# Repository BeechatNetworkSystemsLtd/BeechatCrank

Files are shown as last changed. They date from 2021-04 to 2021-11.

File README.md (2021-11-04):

# Beechat Crank
## _The last charger you'll ever need_

BNSLTD

Beechat Crank is a human-powered, open-hardware, fully-waterproof, electricity generator.
The project was born out of the need to power electronics in all off-grid scenarios. We needed a way to power our devices in all weather conditions, and making a human-powered generator meant that problem could be solved. When we looked for a solution, we didn't find what we were looking for, so we decided to make it, and make it open source!

## Features

- High power (3A) USB-C IPX8 output
- 18650 3600 mAh battery (LG M36)
- Charging time of 4 hrs 24 min. to full charge with 10% efficiency loss at 4.5 Watts.
- Overcharge protection

## Parts

1. Beechat Crank is composed of the main device, which we call the _Heart_. It contains the battery, the generator and all the electronics (the handle is detachable) :
Heart

2. The _Pedal Case_ is an assembly which the _Heart_ can be attached in. which dramatically speeds up the charging from 2.5 hours to 25-30 minutes. This is achieved with reduction gears to, with the same revolutions per minute, generate more electricity.
Heart

## _Generator_ part
We have chosen the 35L048B1B motor with a mass of 88 grams, giving us us 450 mA for each phase of the coil and works at 5V. 
The wire leads are connected via female Molex connectors to the charging PCB board.

## _Heart_ parts

| Part no. | Part name | Quantity | Description | Link | Price |
| --- | --- | --- | --- | --- | --- |
| 01 | Body | 1 | Injection molded ABS/PC |
| 02 |  Lid | 1 | Injection molded ABS/PC
| 03 | Handle | 1 | Injection molded ABS/PC
| 04 | Light pipe | 1 | Transparent injection molded PC
| 05 | Motor | 1 | | [Link](https://aliexpress.com/item/4000827045633.html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,searchweb201602_,searchweb201603_) | $11
| 06 | Bearing | 1 | | [Link](http://manufacturer.ketanbearing.in/70745-NSKF686ADD-Bearing/) | $0.5
| 07 | PCB | 1 | |  | $6
| 08 | Battery holder | 1 | | [Link](https://aliexpress.com/item/4001063295116.html) | $0.09
| 09 | Lid O-Ring | 1 | | [Link]() | $0.95
| 10 | Bearing O-ring | 1 | | [Link](https://www.oringsandmore.com/silicone-o-rings-11-5-x-1mm-minimum-10-pcs/) | $0.08
| 10 | Adhesive | 1 | | | $8.36
| 11 | 10 mm M2 screws | 6 | | |
| 12 | 10 mm M3 screw | 1 | | |
|Total cost (excl. plastic parts and adhesive) | | | | | $18.62 

## _Heart_ PCB parts

All parts are under the "3_BOM and CPL" folder

## _Pedal Case_ parts

| Part no. | Part name | Quantity | Description | Link | Price |
| --- | --- | --- | --- | --- | --- |
| 01 | Sheet metal stand | 1 | Stainless steel sheet metal bend |
| 02 |  Plastic cover | 1 | Injection molded ABS plastic cover
| 03 | 20 teeth spur gear | 1 | Hardened steel-with M3 thread (Custom made)
| 04 | 30/12 teeth double spur gear | 1 | Hardened steel (Custom made)
| 05 | 48 teeth spur gear | 1 | Hardened steel (Custom made)
| 06 | Left pedal crank Arm | 1 | Hardened steel with M8 thread (Custom made) | [Link](https://www.amazon.com/Electric-Bicycle-Conversion-Aluminum-crankset/dp/B083HWCMSR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)
| 07 | Right pedal crank Arm | 1 | Standard part
| 08 | UFL003 bearing | 2 | Standard part | [Link](https://es.aliexpress.com/item/1713738795.html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,searchweb201602_,searchweb201603_)
| 09 | 6mm hollow rod | 1 | with M3 internal thread(Custom made)
| 10 | M6 Washer | 2 | Standard part
| 11 | M3 Washer | 1 | Standard part
| 12 | M7 bolt | 4 | Standard part
| 13 | M3 bolt 15 mm | 3 | Standard part
| 14 | M3 bolt 8 mm | 3 | Standard part
| 15 | M7 nut | 4 | Standard part
| 16 | M3 nut | 3 | Standard part
| 17 | Pedal crank bolt | 2 | Standard part | [Link](https://www.sportwheels.ca/mtb-crank-bolt-crank-nut.html)
| 18 | Pedal | 2 | Standard part | [Link](https://www.amazon.com/BV-Universal-Bicycle-16-Inch-Spindle/dp/B01LYOB0M6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) 

## Development

Want to contribute? Great!

Make a change in the files and create a pull request!

## License

**Open Source Hardware, Non-Commercial**

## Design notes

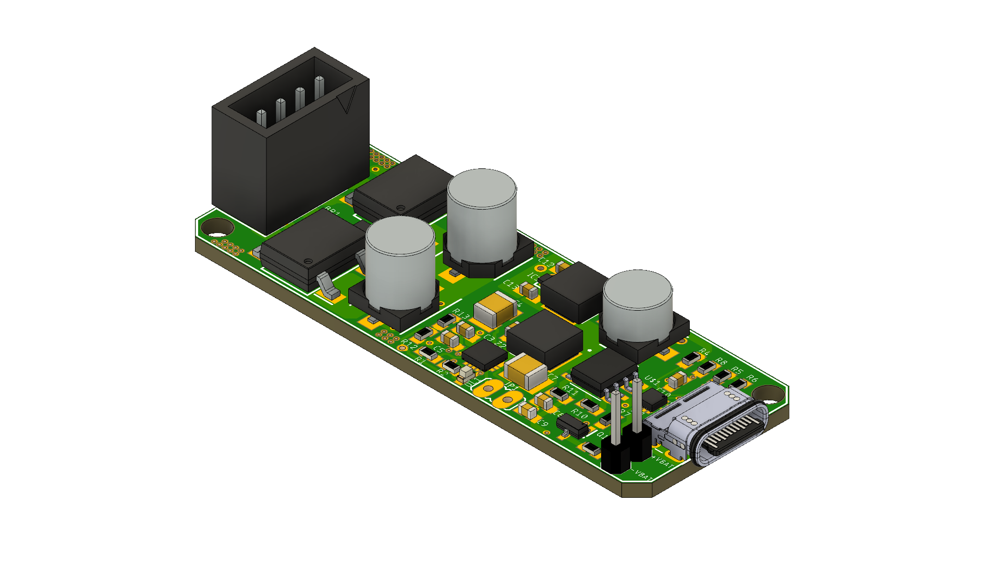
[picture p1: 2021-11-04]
6_ 3D files/Beechat_Crank_v1.2 v4.png

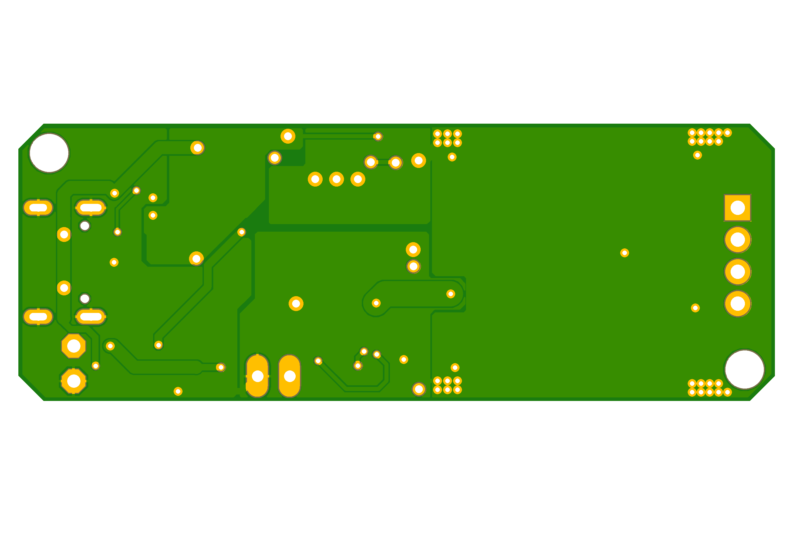
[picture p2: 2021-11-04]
2_ PCB Layout/Beechat_Crank_v1.2_bottom.png

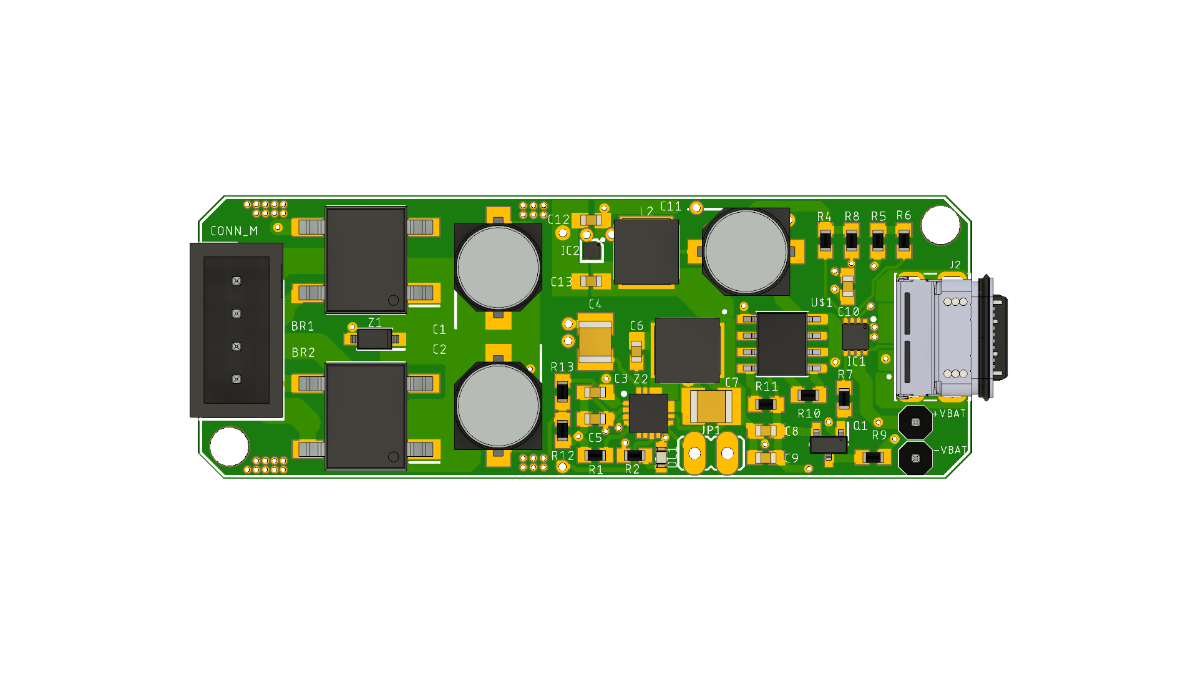
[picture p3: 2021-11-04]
6_ 3D files/Beechat_Crank_v1.2 v4_image2.png

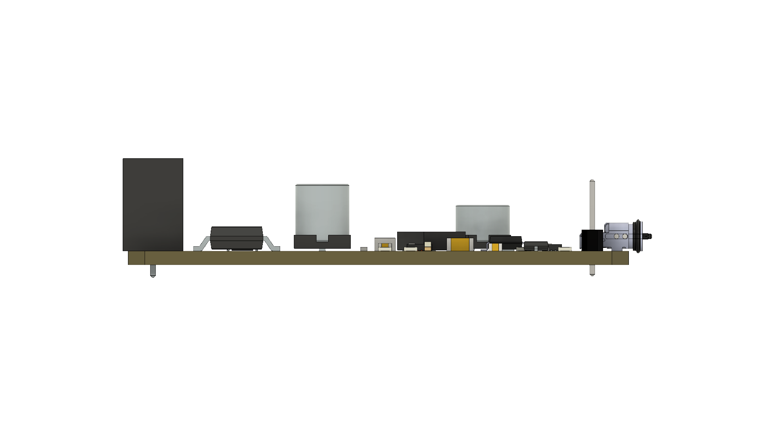
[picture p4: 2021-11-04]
6_ 3D files/Beechat_Crank_v1.2_image3 .png

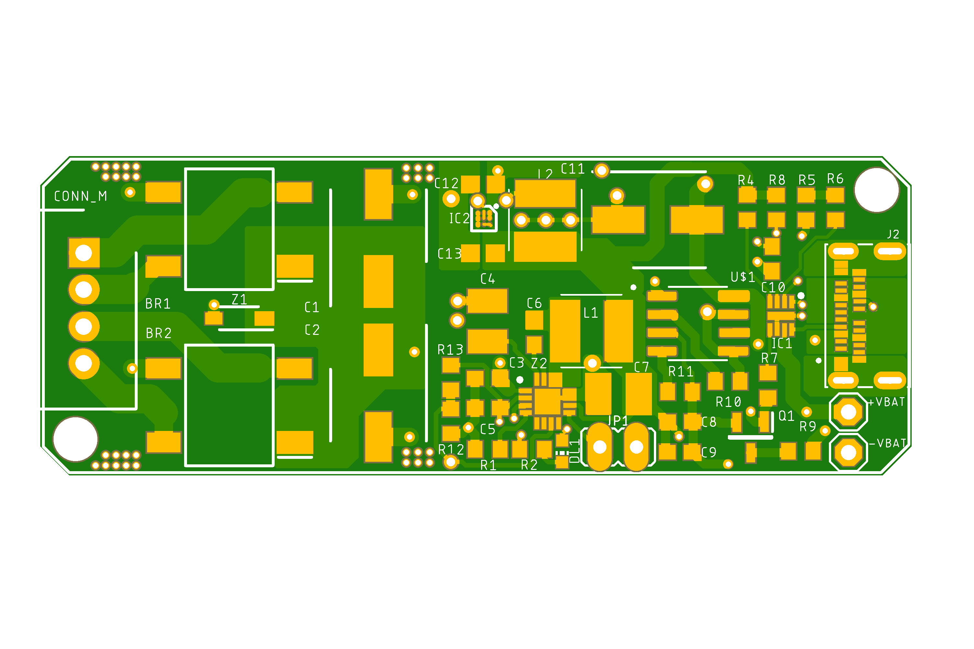
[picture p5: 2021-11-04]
2_ PCB Layout/Beechat_Crank_v1.2_TOP.png

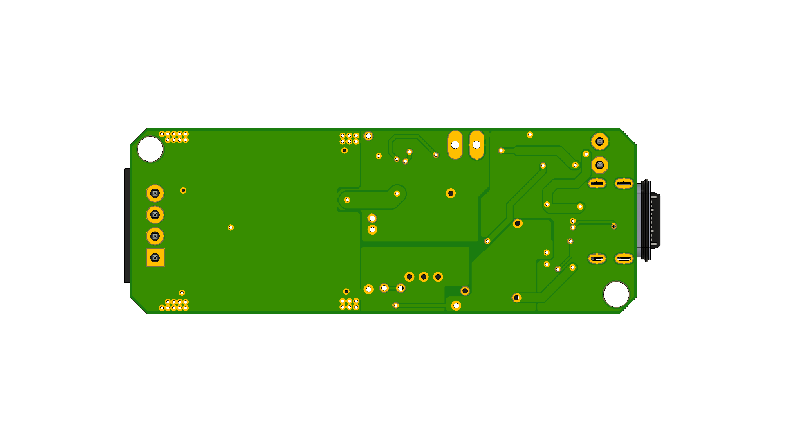
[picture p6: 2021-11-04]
6_ 3D files/Beechat_Crank_v1.2_image4 .png

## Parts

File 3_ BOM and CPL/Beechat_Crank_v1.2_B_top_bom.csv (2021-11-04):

Comment | Designator | Footprint | LCSC Part #
0.1uF | Q1 C10 | C0603
1K | R2 | R0603
1k | R9 | R0603
1uF | L1 L2 | LQH5BPB100MT0L
2.2uF | C3 C5 | C0603
3k | R5 | R0603
4.7uF | C13 | C0603
4.53k | R13 | R0603
5.6V | Z1 | SOD3716X135N
10k | R8 R10 | R0603
10nF | C9 | C0603
10uF | C4 C7 | C1210
10uF | C8 C12 | C0603
13.3k | R1 | R0603
22.6k | R12 | R0603
33uF | C11 | CAPAE660X550N
47nF | C6 | C0603
47uF | C1 C2 | CAPAE660X800N
200k | R4 R7 | R0603
220 | R11 | R0603
887k | R6 | R0603
2305018-2 | J2 | TE_2305018-2
BQ25300RTER | Z2 | QFN50P300X300X80-17N
DF01S-T | BR1 BR2 | SOP510P1040X293-4N
LED_BLUE | DL1 | CHIP-LED0603
MIC2545 | U$1 | SOIC127P599X173-8N
TPS61253YFFT | IC2 | BGA9C40P3X3_121X131X62
TUSB319IDRFRQ1 | IC1 | SON50P200X200X80-9N

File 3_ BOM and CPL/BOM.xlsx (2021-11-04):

Qty | Value | Device | Package | Parts | Manufacturer | #MFR | Description
2 |  | PINHD-1X1 | 1X01 | +VBAT, -VBAT | TE Connectivity | 4-103327-3 | PIN HEADER
1 |  | SI2337DS-T1-BE3 | SOT95P237X112-3N | Q1 | Vishay / Siliconix | SI2337DS-T1-BE3 | MOSFET P-CHANNEL 80-V (D-S)
1 | 0.1uF | C-EUC0603 | C0603 | C10 | Murata Electronics | GCM188R71C104KA37J | CAPACITOR, European symbol
2 | 10k | R_0603 | R0603 | R8, R10 | ROHM Semiconductor | SFR03EZPF1002 | R_0603
1 | 10nF | C-EUC0603 | C0603 | C9 | KEMET | C0603X103K4RACTU | CAPACITOR, European symbol
2 | 10uF | C-EUC0603 | C0603 | C8, C12 | TDK | C1608X5R1C106M080AB | CAPACITOR, European symbol
2 | 10uF | C-EUC1210 | C1210 | C4, C7 | TDK | C3225X8R1C106K250AB | CAPACITOR, European symbol
1 | 13.3k | R_0603 | R0603 | R1 | TE Connectivity | CPF0603F13K3C1 | R_0603
1 | 1K | R_0603 | R0603 | R2 | Panasonic | ERJ-P03J102V | R_0603
1 | 1k | R_0603 | R0603 | R9 | Panasonic (https://ar.mouser.com/manufacturer/panasonicec/) | ERJ-P03J102V | R_0603
2 | 1uF | LQH5BPB1R0NT0L | LQH5BPB100MT0L | L1, L2 | Murata Electronics | LQH5BPB1R0NT0L | LQH5BPB_T0 Series Inductor 1.0uH +/-30% 2020 (5050)
2 | 2.2uF | C-EUC0603 | C0603 | C3, C5 | TDK | C1608X7S1C225K080AE | CAPACITOR, European symbol
2 | 200k | R_0603 | R0603 | R4, R7 | ROHM Semiconductor | ESR03EZPF2003 | R_0603
1 | 22.6k | R_0603 | R0603 | R12 | Bourns | CR0603-FX-2262ELF | R_0603
1 | 220 | R_0603 | R0603 | R11 | Panasonic | ERJ-S03J221V | R_0603
1 | 33uF | 865230343003 | CAPAE660X550N | C11 | Wurth Elektronik | 865230343003 | Wurth Elektronik Aluminium Electrolytic Capacitor 33uF 16V dc 5.5mm V-Chip WCAP-AS5H Series Aluminium, Surface Mount
1 | 3k | R_0603 | R0603 | R5 | Panasonic | ERA-3AED302V | R_0603
1 | 4.53k | R_0603 | R0603 | R13 | Bourns | CR0603-FX-4531ELF | R_0603
1 | 4.7uF | C-EUC0603 | C0603 | C13 | TDK | C1608X5R1C475K080AC | CAPACITOR, European symbol
1 | 47nF | C-EUC0603 | C0603 | C6 | Murata Electronics | GCJ188R71C473KA01D | CAPACITOR, European symbol
2 | 47uF | EEE-HDV470XAP | CAPAE660X800N | C1, C2 | Panasonic | EEE-HDV470XAP | Panasonic 47uF 35V dc Aluminium Electrolytic Capacitor, Surface Mount 6.3 x 7.7mm +105C 6.3mm 7.7mm
1 | 5.6V | MMSZ5V6T3G | SOD3716X135N | Z1 | onsemi | MMSZ5V6T3G | ON Semiconductor MMSZ5V6T3G Zener Diode, 5.6V 5% 0.5 W SMT 2-Pin SOD-123
1 | 887k | R_0603 | R0603 | R6 | Bourns (https://ar.mouser.com/manufacturer/bourns/) | CR0603-FX-8873ELF | R_0603
1 | 90136-1304 | 90136-1304 | SHDR4W65P0X254_1X4_1351X721X11 | CONN_M | Molex | 90136-1304 | Headers & Wire Housings C-Grid Shrd Hdr SR V Hdr SR Vt Au-F 4Ckt
1 | BQ25300RTER | BQ25300RTER | QFN50P300X300X80-17N | Z2 | Texas Instruments (https://ar.mouser.com/manufacturer/texas-instruments/) | BQ25300RTER | Battery Management Standalone 1-cell, 17-V, 3.0-A battery charger 16-WQFN -40 to 85
2 | DF01S-T | DF01S-T | SOP510P1040X293-4N | BR1, BR2 | Diodes incorporation | DF01S-T | 100V 1.0A SURFACE MOUNT GLASS PASSIVATED BRIDGE RECTIFIER
1 | LED_BLUE | LEDSMD0603 | CHIP-LED0603 | DL1 | Wurth Elektronik | 150060BS75000 | LED_0603
1 | MIC2545 | MIC2545 | SOIC127P599X173-8N | U$1 | Microchip | MIC2545 | MIC2545 POWER SWICTH
1 | TPS61253YFFT | TPS61253YFFT | BGA9C40P3X3_121X131X62 | IC2 | Texas Instruments | TPS61253YFFT | 3.5MHz, 1500mA peak loading current, high efficiency step-up converter in chip scale packaging
1 | TUSB319IDRFRQ1 | TUSB319IDRFRQ1 | SON50P200X200X80-9N | IC1 | Texas Instruments | TUSB319IDRFRQ1 | Automotive USB Type-C DFP Port Controller
1 | USB4105-GF-A | USB4105-GF-A | GCT_USB4105-GF-A | J1 | GCT | USB4105-GF-A | USB-C (USB TYPE-C) USB 2.0 Receptacle Connector 24 (16+8 Dummy) Position Surface Mount, Right Angle; Through Hole Check prices

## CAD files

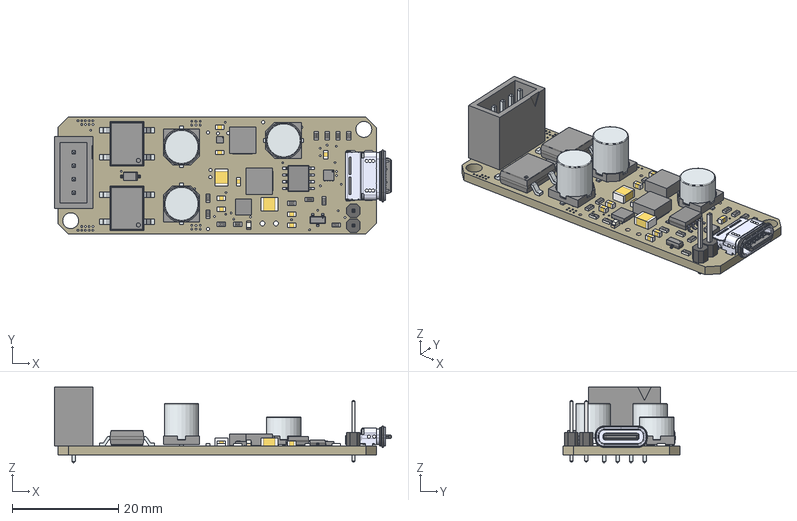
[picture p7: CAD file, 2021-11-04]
6_ 3D files/Beechat_Crank_v1.2_.step
63.4 x 22.0 x 14.3 mm
Board
1X01 x 2
PinsArrayLR x 2
Base x 2
Pin1Fillet x 2
Pin2Fillet x 2
10nF x 8
Base (1)
Pin1Fillet (1)
Pin2Fillet (1)
10uF x 2
LeadsArray
LED_BLUE
ThermalPin
PinsArrayLR (1)
Pins x 2
PinsArrayL
FilletPinR
1k x 12
MIC2545
FilletPinL
FilletPinR (1)
BODY-QFN
FRAME-RTE0016C
JP1

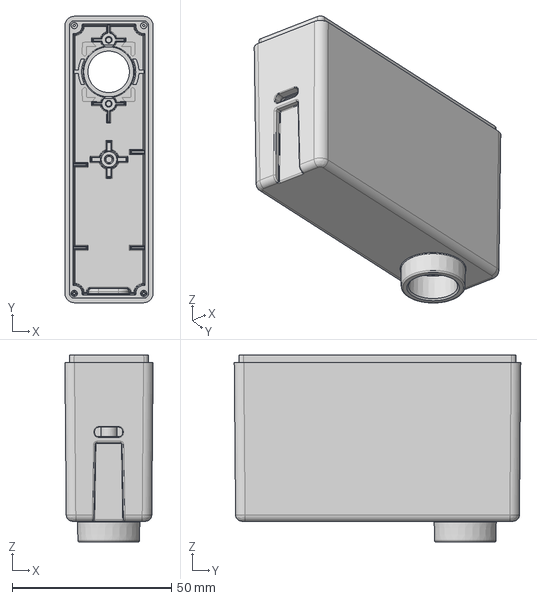
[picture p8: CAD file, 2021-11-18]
Enclosure_STEP_Files/Body.step
27.7 x 89.9 x 58.7 mm

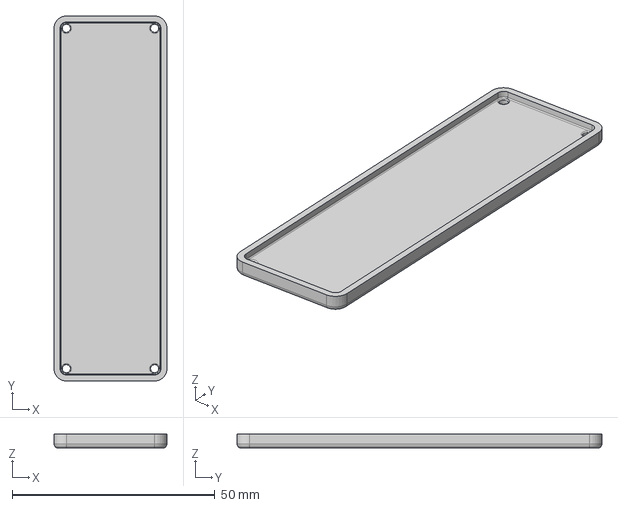
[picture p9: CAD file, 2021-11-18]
Enclosure_STEP_Files/Lid.step
27.9 x 90.1 x 3.50 mm

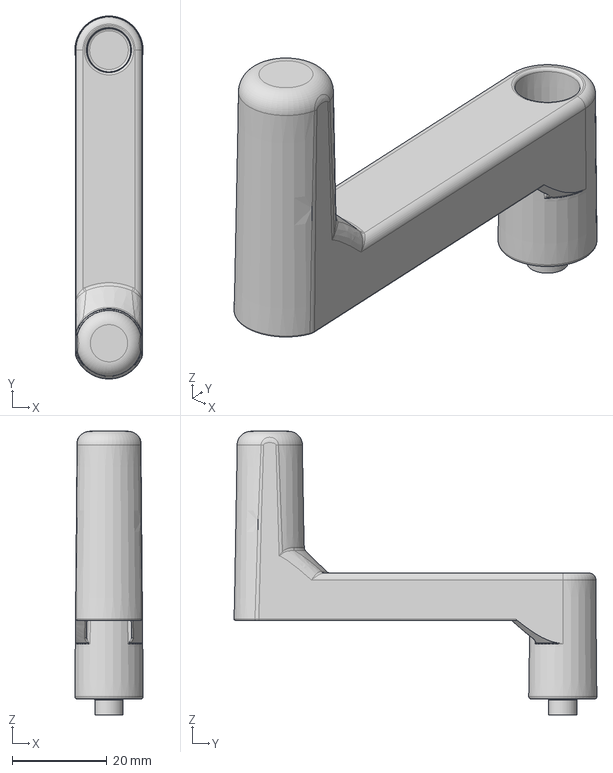
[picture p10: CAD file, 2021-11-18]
Enclosure_STEP_Files/Handle.step
14.5 x 76.8 x 60.0 mm

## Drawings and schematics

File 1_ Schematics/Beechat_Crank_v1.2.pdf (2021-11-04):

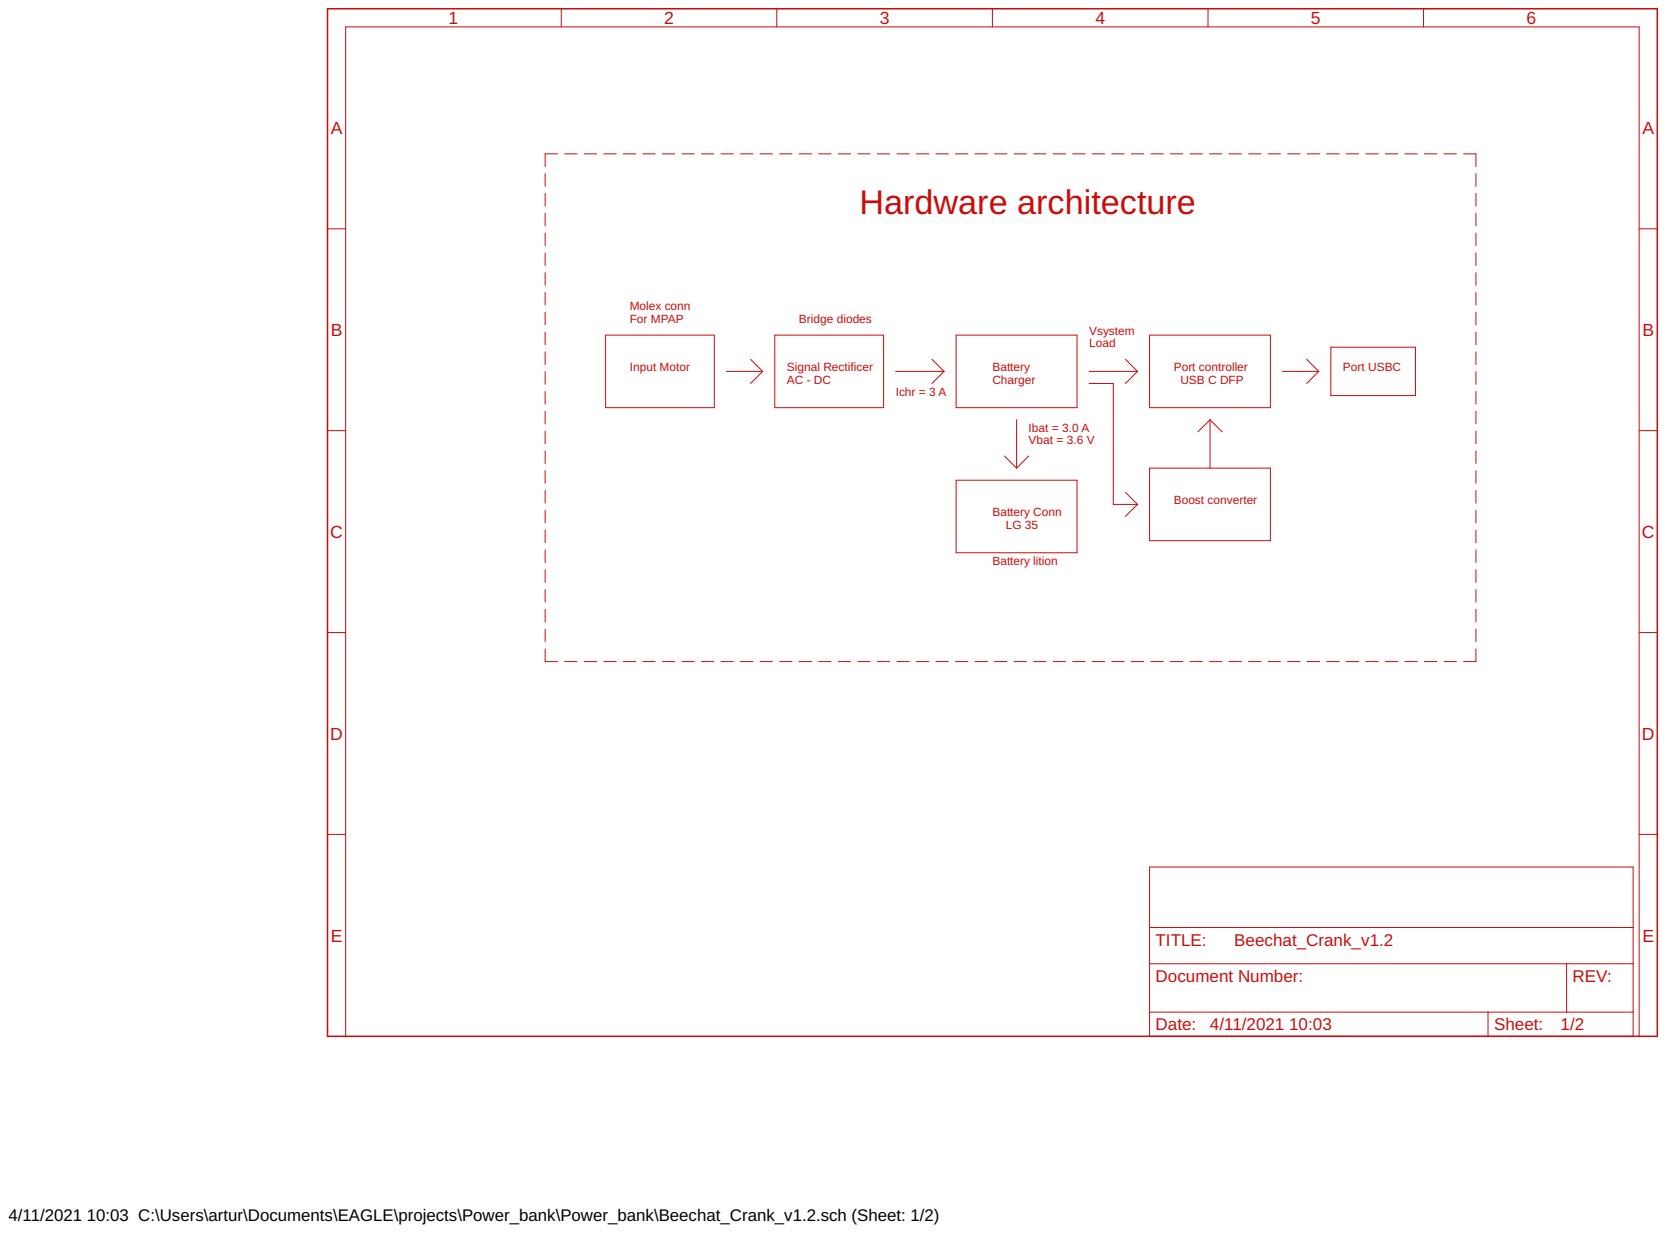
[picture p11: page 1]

Input Motor Molex conn For MPAP

Signal Rectificer AC - DC

Port controller USB C DFP

Document Number: | REV:

Date: 4/11/2021 10:03 | Sheet: 1/2

4/11/2021 10:03 C:\Users\artur\Documents\EAGLE\projects\Power_bank\Power_bank\Beechat_Crank_v1.2.sch (Sheet: 1/2)

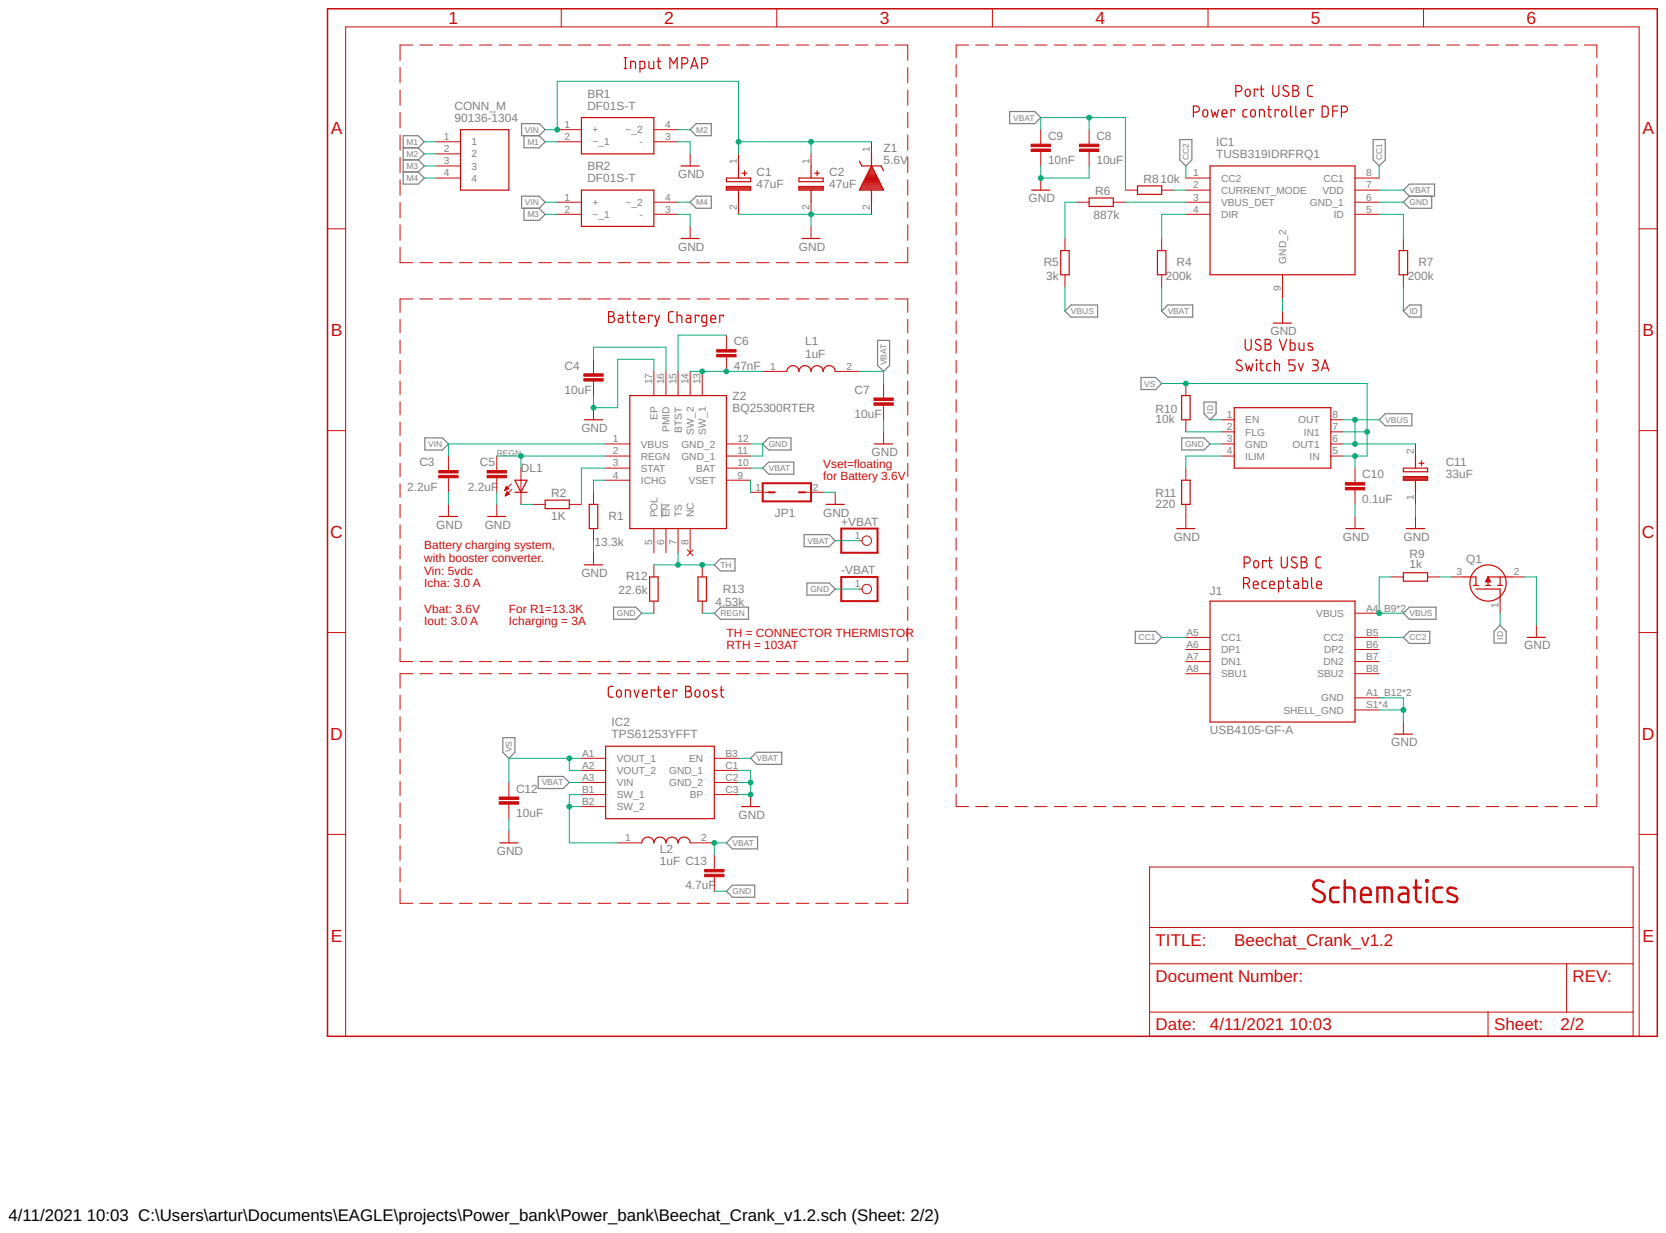
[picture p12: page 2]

Battery charging system, with booster converter. Vin: 5vdc

Document Number: | REV:

Date: 4/11/2021 10:03 | Sheet: 2/2

4/11/2021 10:03 C:\Users\artur\Documents\EAGLE\projects\Power_bank\Power_bank\Beechat_Crank_v1.2.sch (Sheet: 2/2)

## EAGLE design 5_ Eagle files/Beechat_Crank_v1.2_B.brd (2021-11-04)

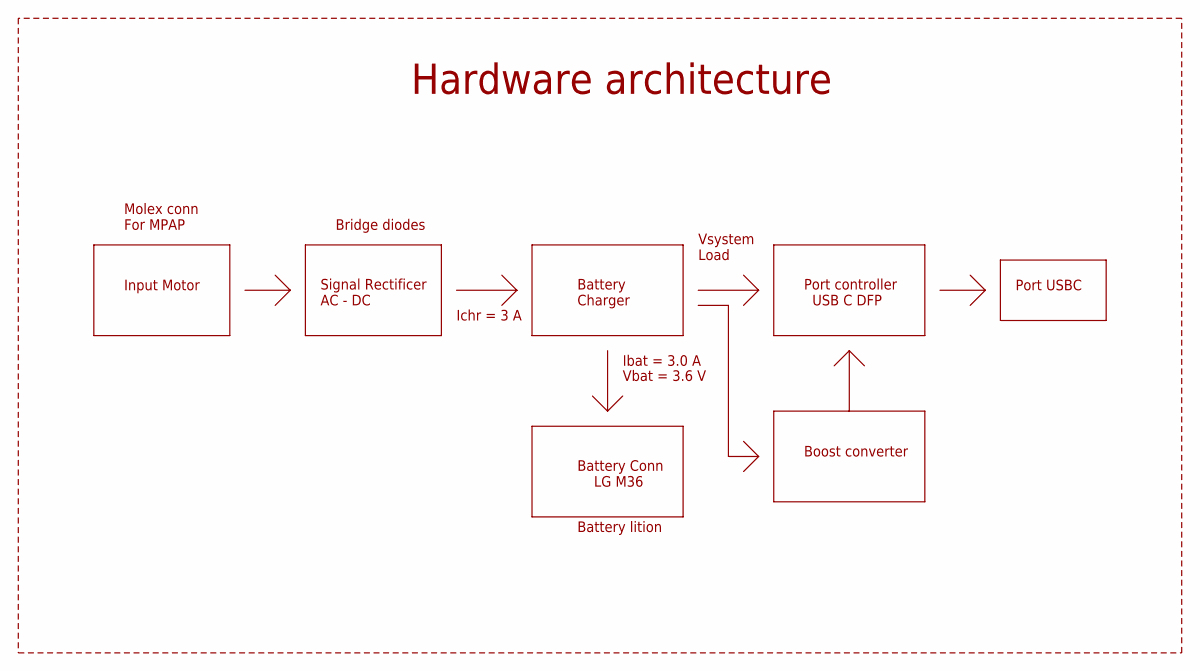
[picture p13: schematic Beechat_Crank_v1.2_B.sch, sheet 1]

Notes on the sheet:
Hardware architecture
Input Motor
Molex conn For MPAP
Signal Rectificer AC - DC
Bridge diodes
Battery Charger
Battery Conn LG M36
Ibat = 3.0 A
Ichr = 3 A
Battery lition
Vbat = 3.6 V
Port controller USB C DFP
Vsystem Load
Port USBC
Boost converter

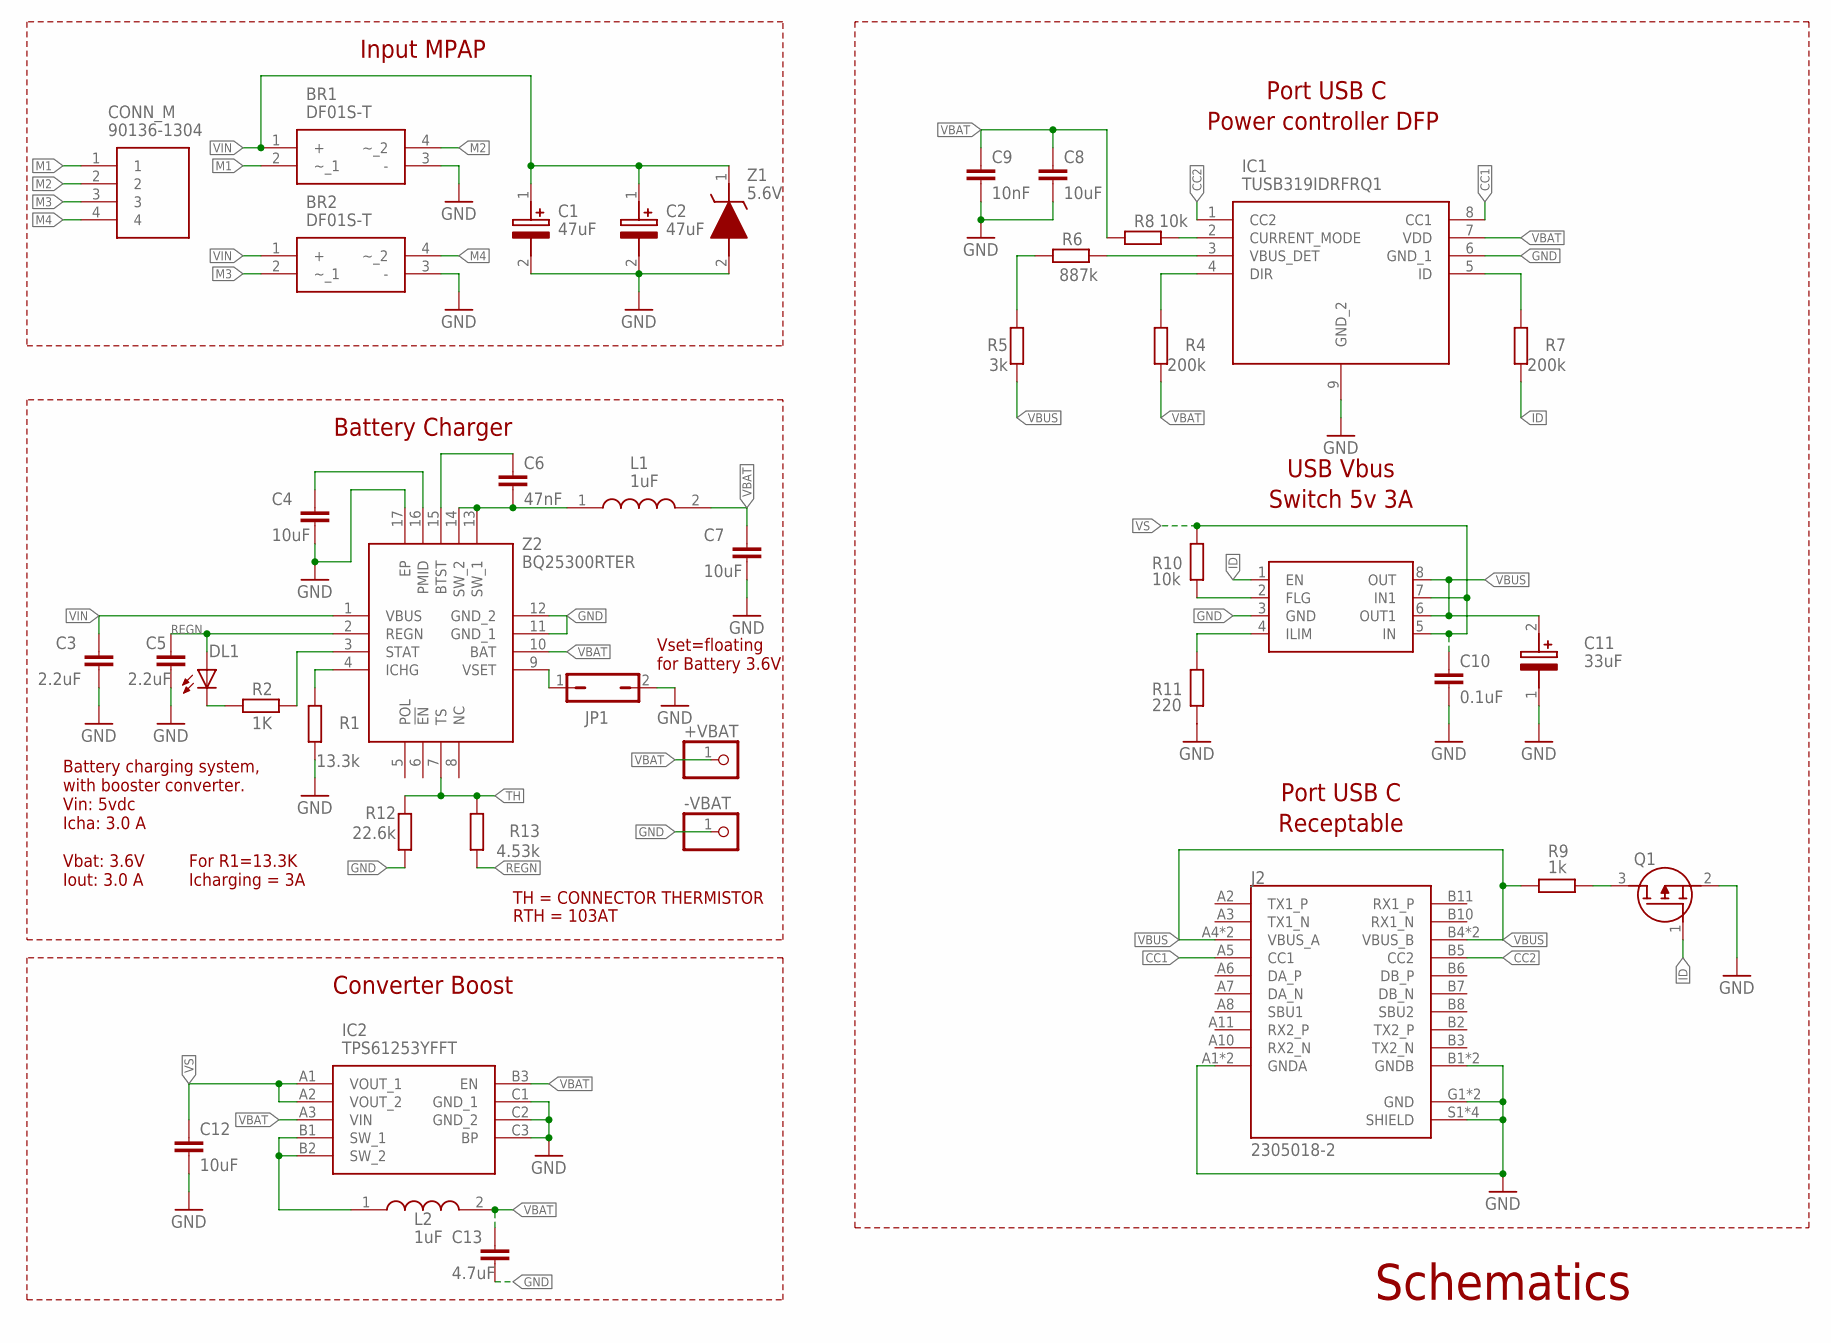
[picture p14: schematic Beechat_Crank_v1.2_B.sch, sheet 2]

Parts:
+VBAT: PINHD-1X1; 1X01
-VBAT: PINHD-1X1; 1X01
BR1, BR2: DF01S-T; SOP510P1040X293-4N
C1, C2: 47uF; CAPAE660X800N
C3, C5: 2.2uF; C0603
C4, C7: 10uF; C1210
C6: 47nF; C0603
C8, C12: 10uF; C0603
C9: 10nF; C0603
C10: 0.1uF; C0603
C11: 33uF; CAPAE660X550N
C13: 4.7uF; C0603
CONN_M: 90136-1304; SHDR4W65P0X254_1X4_1351X721X11
DL1: LED_BLUE; CHIP-LED0603
IC1: TUSB319IDRFRQ1; SON50P200X200X80-9N
IC2: TPS61253YFFT; BGA9C40P3X3_121X131X62
J2: 2305018-2; TE_2305018-2
JP1: JP1Q; JP1
L1, L2: 1uF; LQH5BPB100MT0L
Q1: SI2337DS-T1-BE3; SOT95P237X112-3N
R1: 13.3k; R0603
R2: 1K; R0603
R4, R7: 200k; R0603
R5: 3k; R0603
R6: 887k; R0603
R8, R10: 10k; R0603
R9: 1k; R0603
R11: 220; R0603
R12: 22.6k; R0603
R13: 4.53k; R0603
U$1: MIC2545; SOIC127P599X173-8N
Z1: 5.6V; SOD3716X135N
Z2: BQ25300RTER; QFN50P300X300X80-17N

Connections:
CC1: IC1.8 (CC1), J2.A5 (CC1)
CC2: IC1.1 (CC2), J2.B5 (CC2)
GND: -VBAT.1, BR1.3 (-), BR2.3 (-), C1.2 (-), C2.2 (-), C3.2, C4.2, C5.2, C7.2, C8.2, C9.2, C10.2, C11.1 (-), C12.2, C13.2, IC1.6 (GND_1), IC1.9 (GND_2), IC2.C1 (GND_1), IC2.C2 (GND_2), IC2.C3 (BP), J2.A1 (GNDA), J2.A12 (GNDA), J2.B1 (GNDB), J2.B12 (GNDB), J2.G1 (GND), J2.G2 (GND), J2.S1 (SHIELD), J2.S2 (SHIELD), J2.S3 (SHIELD), J2.S4 (SHIELD), JP1.2, Q1.2 (S), R1.1, R11.2, R12.1, U$1.3 (GND), Z1.2 (A), Z2.11 (GND_1), Z2.12 (GND_2), Z2.17 (EP)
ID: Q1.1 (G), R7.1, U$1.1 (EN)
M1: BR1.2 (~_1), CONN_M.1
M2: BR1.4 (~_2), CONN_M.2
M3: BR2.2 (~_1), CONN_M.3
M4: BR2.4 (~_2), CONN_M.4
unnamed: JP1.1, Z2.9 (VSET)
unnamed: R1.2, Z2.4 (ICHG)
unnamed: DL1.C, R2.2
unnamed: C4.1, Z2.16 (PMID)
unnamed: R2.1, Z2.3 (STAT)
unnamed: C6.1, Z2.15 (BTST)
unnamed: C6.2, L1.1, Z2.13 (SW_1), Z2.14 (SW_2)
unnamed: IC1.3 (VBUS_DET), R6.1
unnamed: R5.2, R6.2
unnamed: IC1.4 (DIR), R4.2
unnamed: IC1.5 (ID), R7.2
unnamed: R10.2, U$1.2 (FLG)
unnamed: IC1.2 (CURRENT_MODE), R8.1
unnamed: IC2.B1 (SW_1), IC2.B2 (SW_2), L2.1
unnamed: Q1.3 (D), R9.1
unnamed: R11.1, U$1.4 (ILIM)
REGN: C5.1, DL1.A, R13.1, Z2.2 (REGN)
TH: R12.2, R13.2, Z2.7 (TS)
VBAT: +VBAT.1, C7.1, C8.1, C9.1, C13.1, IC1.7 (VDD), IC2.A3 (VIN), IC2.B3 (EN), L1.2, L2.2, R4.1, R8.2, Z2.10 (BAT)
VBUS: C11.2 (+), J2.A4 (VBUS_A), J2.A9 (VBUS_A), J2.B4 (VBUS_B), J2.B9 (VBUS_B), R5.1, R9.2, U$1.6 (OUT1), U$1.8 (OUT)
VIN: BR1.1 (+), BR2.1 (+), C1.1 (+), C2.1 (+), C3.1, Z1.1 (K), Z2.1 (VBUS)
VS: C10.1, C12.1, IC2.A1 (VOUT_1), IC2.A2 (VOUT_2), R10.1, U$1.5 (IN), U$1.7 (IN1)

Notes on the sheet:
Input MPAP
Battery charging system, with booster converter. Vin: 5vdc Icha: 3.0 A Vbat: 3.6V Iout: 3.0 A
Battery Charger
Port USB C Receptable
USB Vbus Switch 5v 3A
Port USB C Power controller DFP
Schematics
For R1=13.3K Icharging = 3A
TH = CONNECTOR THERMISTOR
RTH = 103AT
Vset=floating for Battery 3.6V
Converter Boost

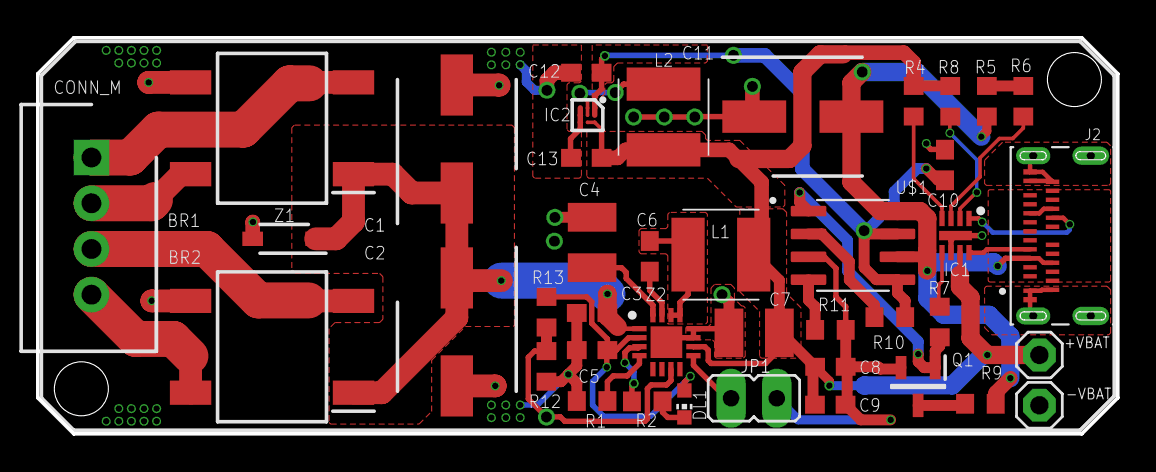
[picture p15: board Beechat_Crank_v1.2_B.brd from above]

Board: 2 copper layers, 60.0 x 22.0 mm, 41 parts (0 on the bottom side), 30 nets.

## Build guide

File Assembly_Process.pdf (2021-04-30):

## Assembly Process

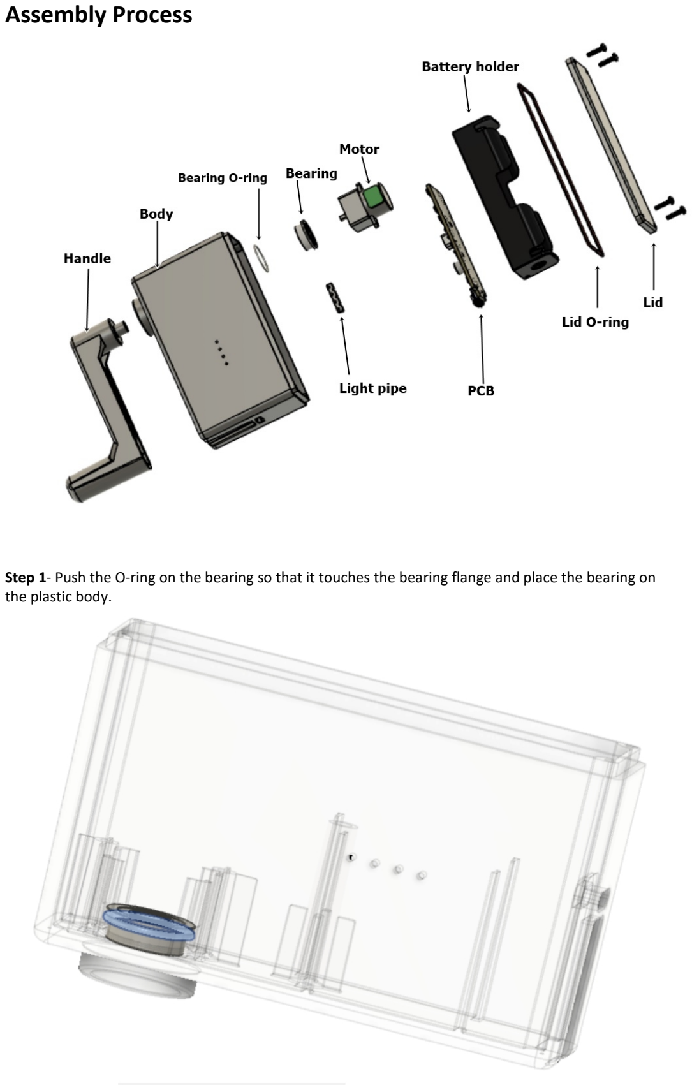
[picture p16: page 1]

Step 1- Push the O-ring on the bearing so that it touches the bearing flange and place the bearing on the plastic body.

Step 2- Solder the motors wires on the PCB and place them on the plastic body. Use two M2 screws to fix it.

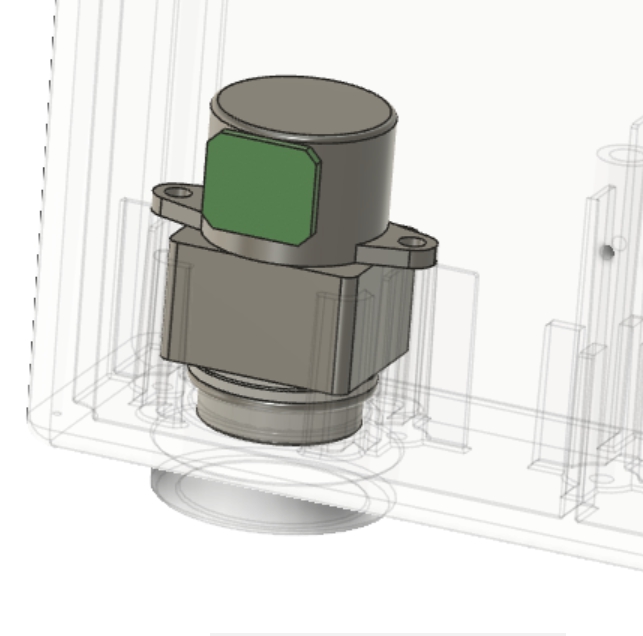
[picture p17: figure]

Step 3- Push the handle in so that it grips the motor shaft.

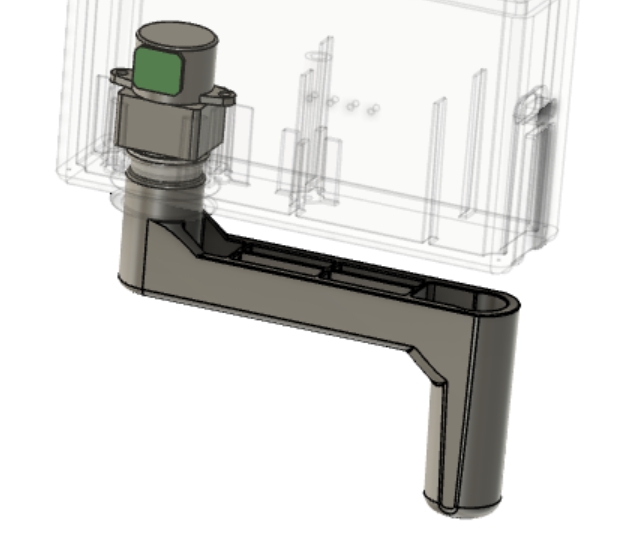
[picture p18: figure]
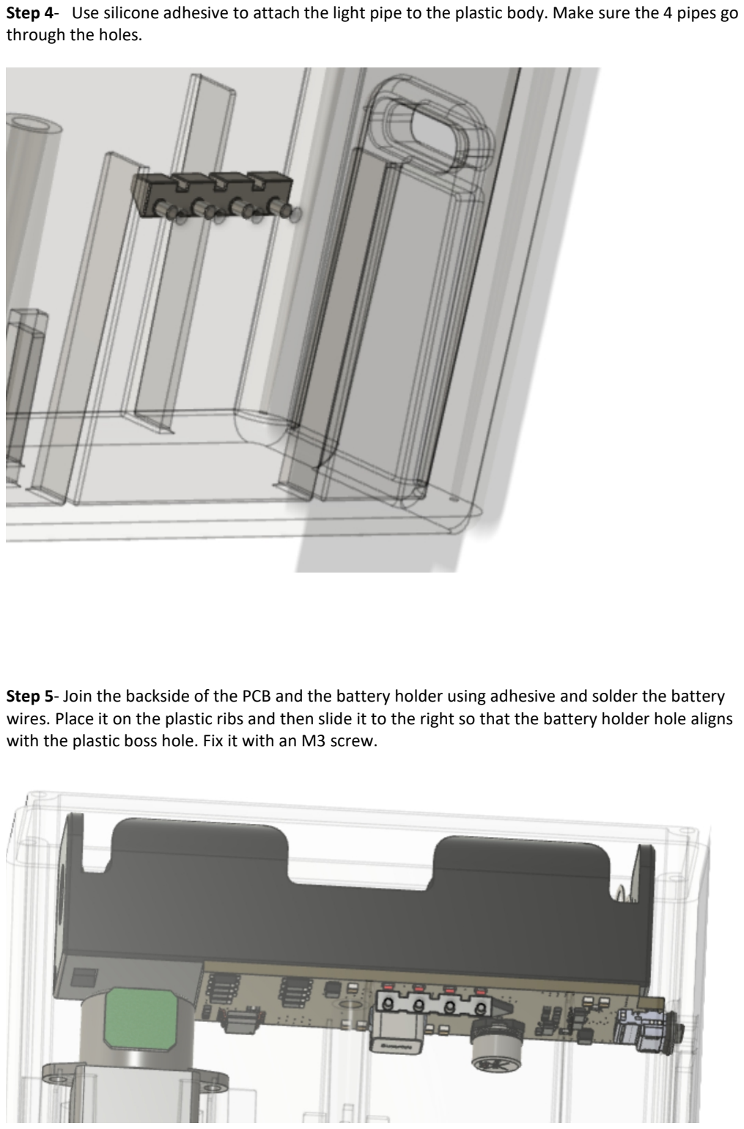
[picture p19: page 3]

Step 4- Use silicone adhesive to attach the light pipe to the plastic body. Make sure the 4 pipes go through the holes.
Step 5- Join the backside of the PCB and the battery holder using adhesive and solder the battery wires. Place it on the plastic ribs and then slide it to the right so that the battery holder hole aligns with the plastic boss hole. Fix it with an M3 screw.

Step 6 - Put the O-ring on the body top and close the lid using 4 M2 screws.

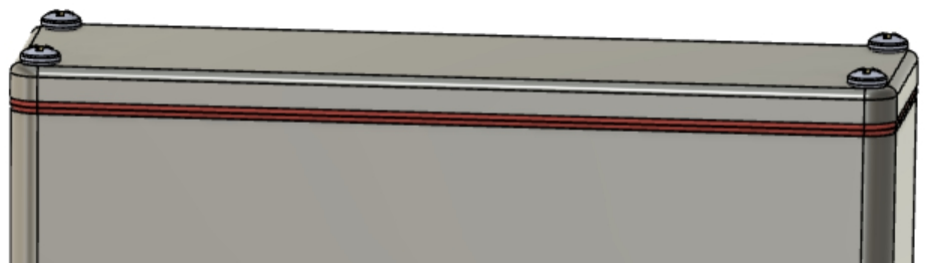
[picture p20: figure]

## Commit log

2021-04-30 Added Assembly Process PDF
2021-11-04 Beechat Crank V1.2 Update
    We can now configure the voltage of the battery that we want to use, by default the chosen LG M36 battery provides 3.6v 3A, but then with a jumper we can configure the value and change the battery if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
    [BOM.xlsx, Beechat_Crank_v1.2_.step, Beechat_Crank_v1.2_B.brd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]
